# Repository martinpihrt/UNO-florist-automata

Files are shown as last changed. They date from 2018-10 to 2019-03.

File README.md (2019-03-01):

UNO florist automata Readme  
====

## UNO florist automata - Zavlažovač květin je založený na platformě Arduino a desce Arduino UNO<br>
(procesor ATMEGA328 a vlastní deska spojů)

Celý projekt je založen jako volný zdroj (lze použít pro nekomerční použití a přizpůsobit si k obrazu svému).<br>
K řídící desce je připojeno teplotní čidlo DS18B20, které měří teplotu půdy (pro možnost regulace zavlažování dle teploty)<br>
K řídící desce je také připojeno čidlo vlhkosti s frekvenčním výstupem 50Hz-5kHz (pro možnost regulace zavlažování dle vlhkosti) https://pihrt.com/elektronika/272-snimac-vlhkosti-pro-zalevaci-automat<br>
Veškeré nastavení automatu se provádí pomocí tlačítek a zobrazení údajů na 16x2 LCD displeji.<br>
Automat byl vyvinutý pro vertikální zavlažování rostlin, které má svá specifika zavlažování.<br>

## Pro více informací navštivte web...
Martin Pihrt - www.pihrt.com: https://pihrt.com/elektronika/400-uno-florist-automata<br>

## Pohled na desku a připojení čidel
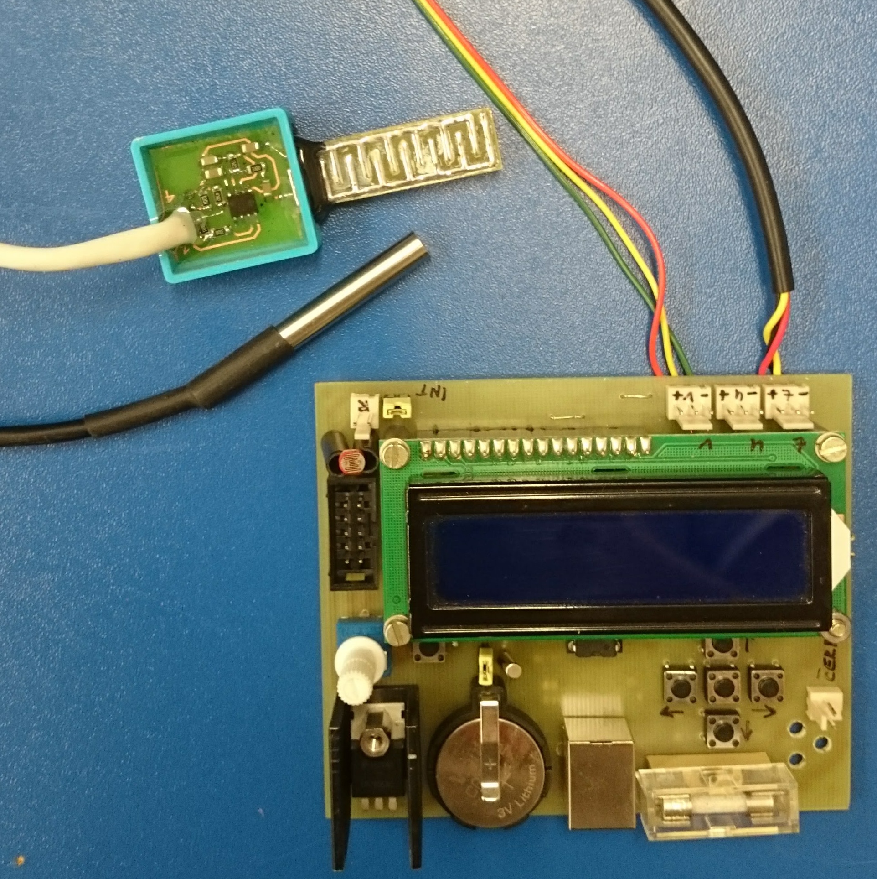
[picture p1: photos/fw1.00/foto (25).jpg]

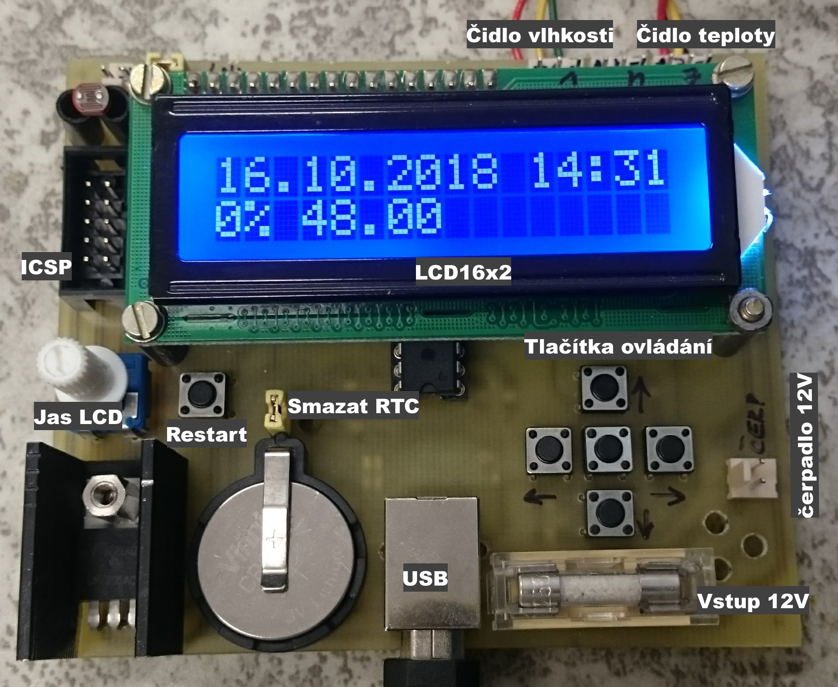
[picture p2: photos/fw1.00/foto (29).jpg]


## Video (fw 1.00 beta)
Ukázka chodu (https://www.pihrt.com/images/videa/automata_1.00.mp4)

## Nastavení zavlažování dle dnů od pondělí do neděle
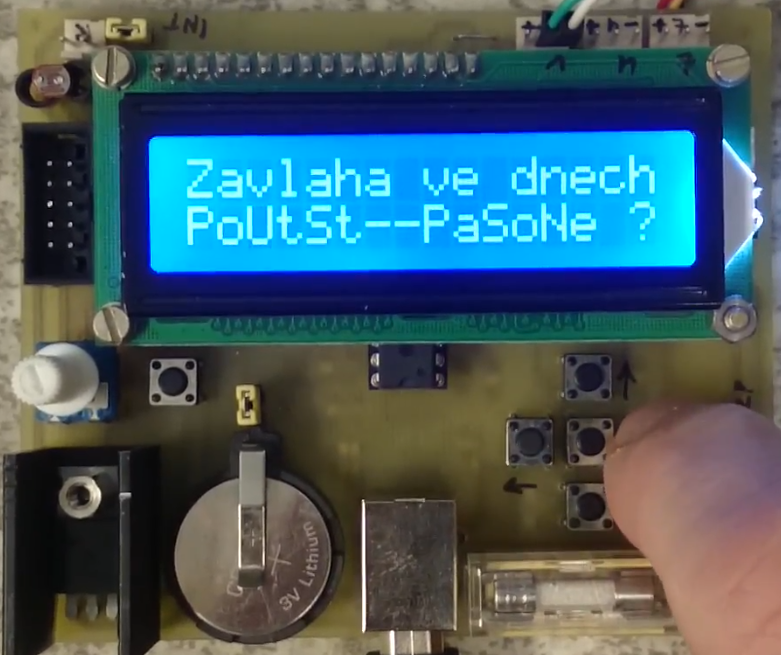
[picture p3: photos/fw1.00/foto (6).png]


## Nastavení 3 nezávislých časů pro zavlažování s různou dobou provozu čerpadla
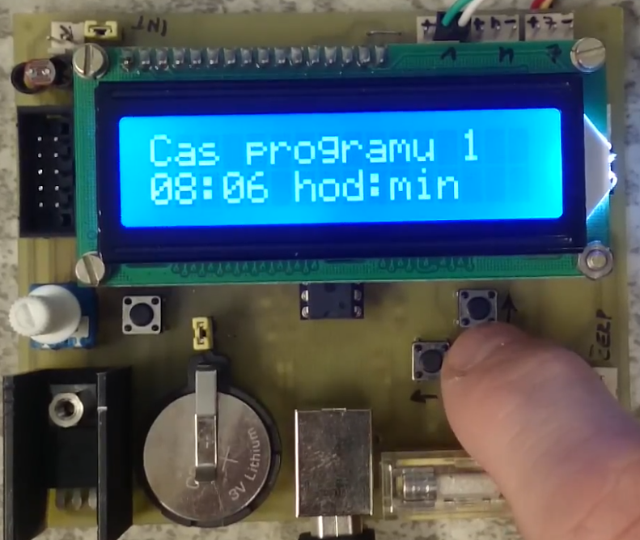
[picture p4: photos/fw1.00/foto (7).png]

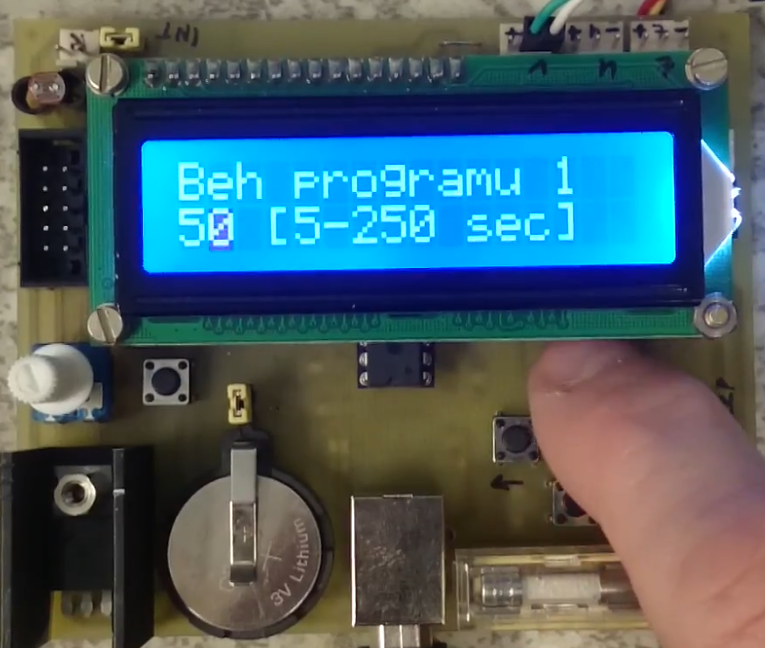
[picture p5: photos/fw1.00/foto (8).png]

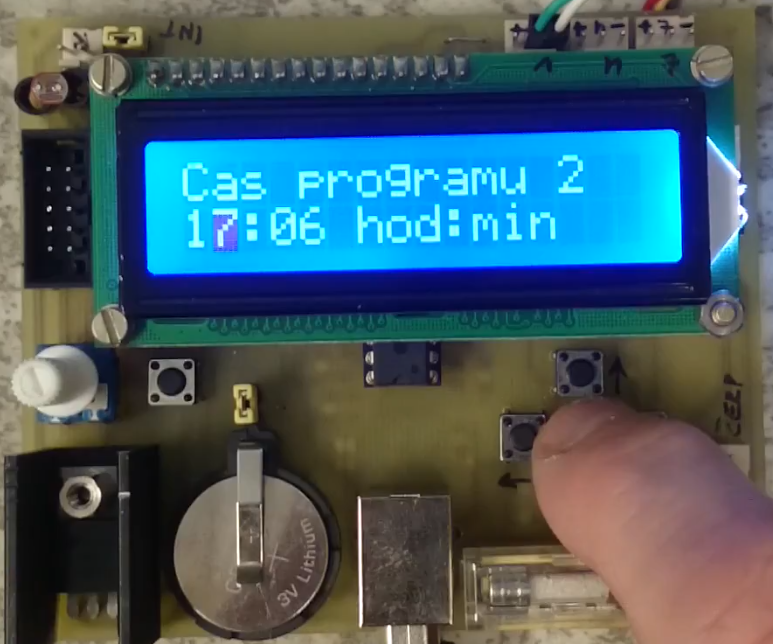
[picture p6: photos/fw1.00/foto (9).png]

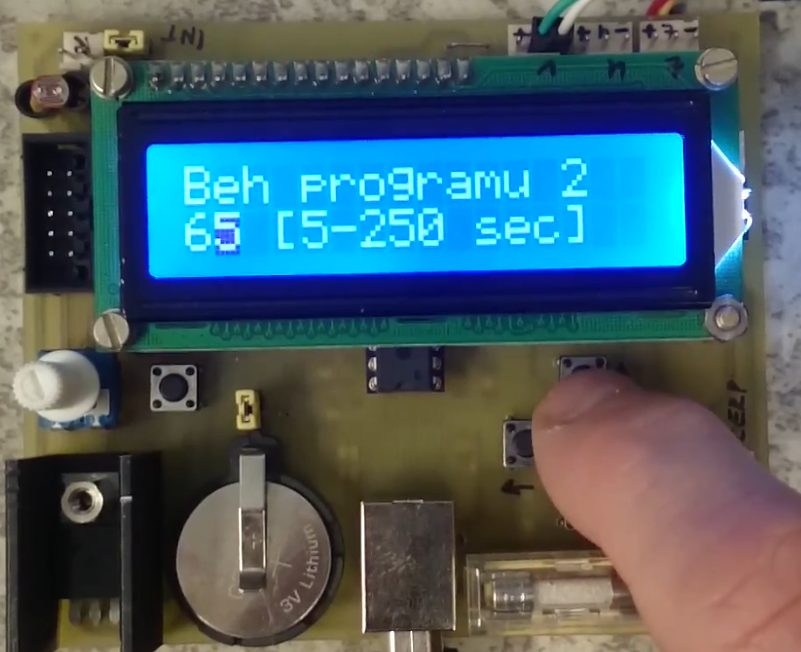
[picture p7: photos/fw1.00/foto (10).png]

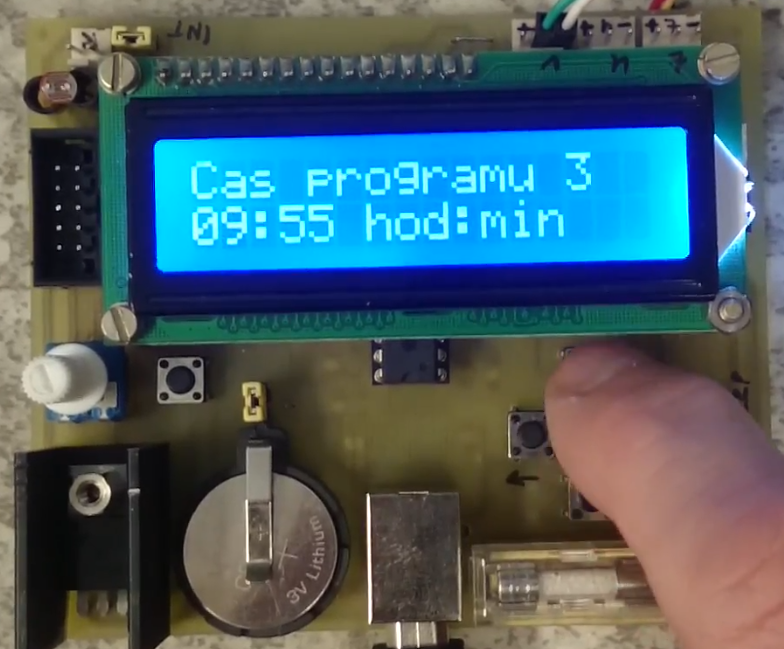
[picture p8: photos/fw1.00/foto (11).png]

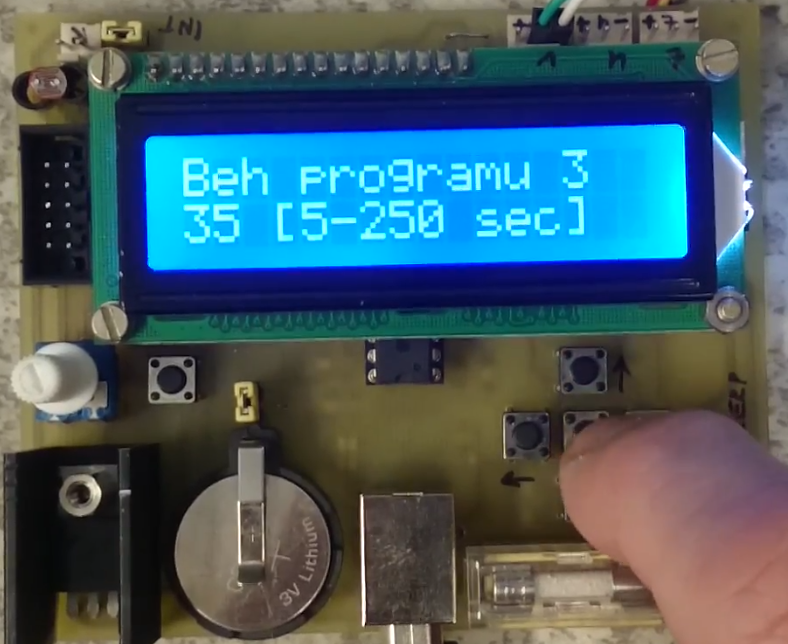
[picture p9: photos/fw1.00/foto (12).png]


## Regulace dle vlhkosti
a) pokud je daný den a je čas programu 1 nebo je čas programu 2 nebo je čas programu 3 a vlhkost < 40% bude výsledná doba trvání závlahy + 1/2 trvání závlahy nastavené doby v menu. Tj. 150% času.<br>
b) pokud je daný den a je čas programu 1 nebo je čas programu 2 nebo je čas programu 3 a vlhkost >= 40% a < 60% bude výsledná doba trvání závlahy stejná jako nastavená doba v menu. Tj. 100% času.<br>
c) pokud je daný den a je čas programu 1 nebo je čas programu 2 a vlhkost >= 60% a < 80% bude výsledná doba trvání závlahy stejná jako nastavená doba v menu. Tj. 100% času.<br>
d) pokud je daný den a je čas programu 1 a vlhkost >= 60% bude výsledná doba trvání závlahy stejná jako nastavená doba v menu. Tj. 100% času.<br>
Z výše uvedeného vyplývá, že některé programy se s ohledem na vlhkost v určitém rozsahu vůbec nespustí, nebo bude výsledný čas upraven.<br>
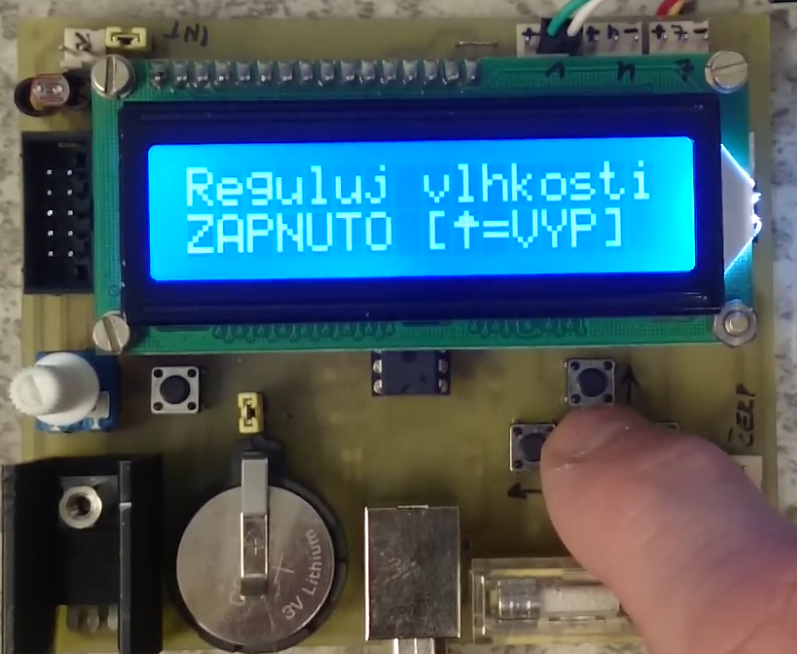
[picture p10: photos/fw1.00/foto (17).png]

<b>V žádném případě nepoužívejte obě regulace současně!</b>

## Regulece dle teploty
a) pokud je daný den a je čas programu 1 nebo je čas programu 2 nebo je čas programu 3 a teplota > 40°C bude výsledná doba trvání závlahy + 1/2 trvání závlahy nastavené doby v menu. Tj. 150% času.<br>
b) pokud je daný den a je čas programu 1 nebo je čas programu 2 nebo je čas programu 3 a teplota >= 30°C a < 40°C bude výsledná doba trvání závlahy stejná jako nastavená doba v menu. Tj. 100% času.<br>
c) pokud je daný den a je čas programu 1 nebo je čas programu 2 a teplota >= 20°C a < 30°C bude výsledná doba trvání závlahy stejná jako nastavená doba v menu. Tj. 100% času.<br>
d) pokud je daný den a je čas programu 1 a teplota >= 5°C a < 20°C bude výsledná doba trvání závlahy stejná jako nastavená doba v menu. Tj. 100% času.<br>
Z výše uvedeného vyplývá, že některé programy se s ohledem na teplotu v určitém rozsahu vůbec nespustí, nebo bude výsledný čas upraven.<br>
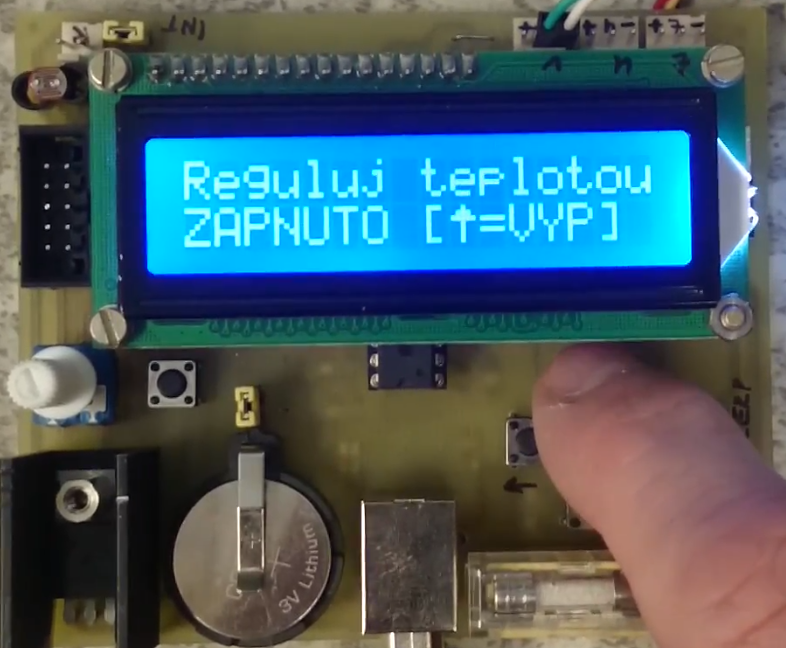
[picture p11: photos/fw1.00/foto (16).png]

<b>V žádném případě nepoužívejte obě regulace současně!</b>

## Cyklování výstupu
V menu lze nastavit po jaké době běhu programu (1, 2, 3) se má výstup čerpadla vypnout a jako dobu má čekat vypnutý. Tato funkce umožňuje cyklování výstupu pro lepší vsakování vody do půdy (nedojde k přetékání květináče, ale k postupnému vsaku vody)<br>
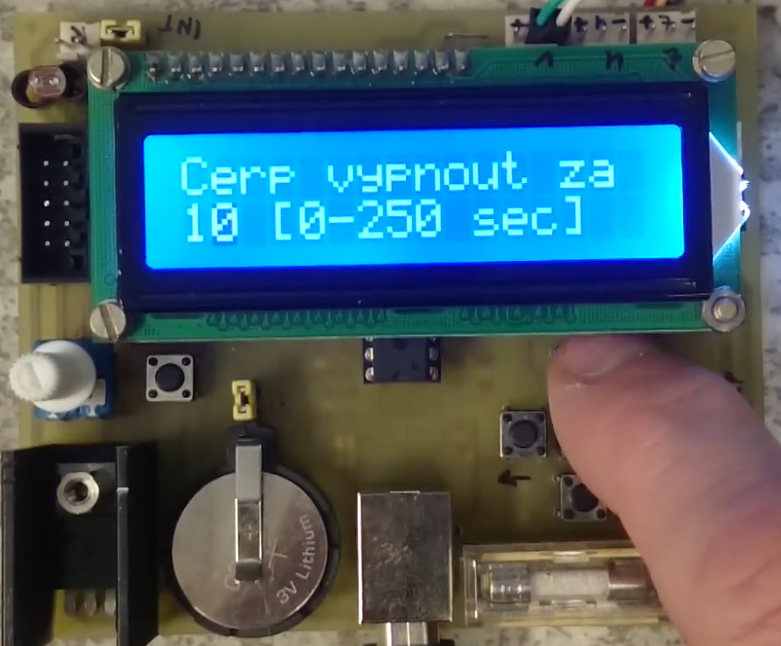
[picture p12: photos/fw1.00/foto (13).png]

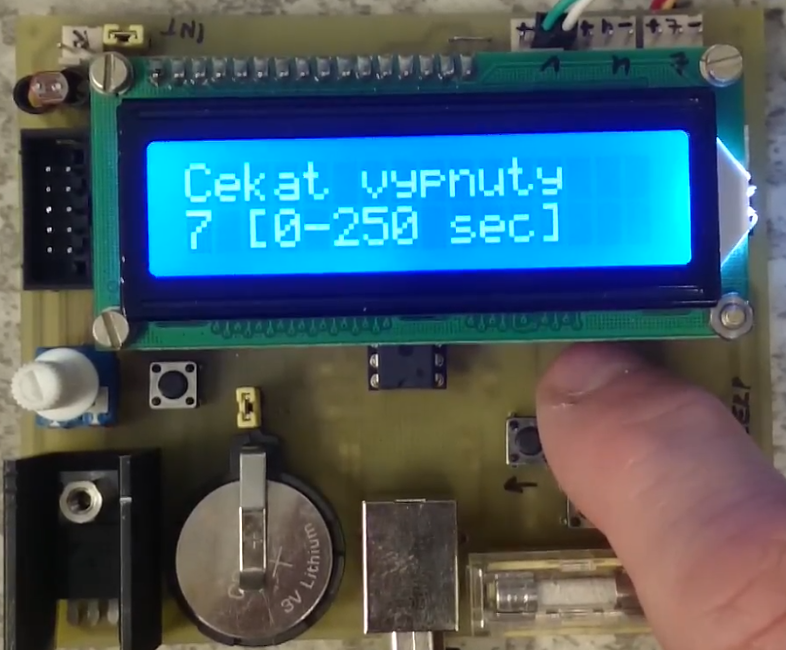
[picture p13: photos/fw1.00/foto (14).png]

Pokud nepožadujeme funkci cyklování nastavíme v menu "vypnout na dobu" na hodnotu 0s" a "vypnout čerpadlo po" na maximální hodnotu 250s.<br>
V grafu je vidět spínání výstupu (zap/vyp cyklování) s ohledem na vlhkost.<br>
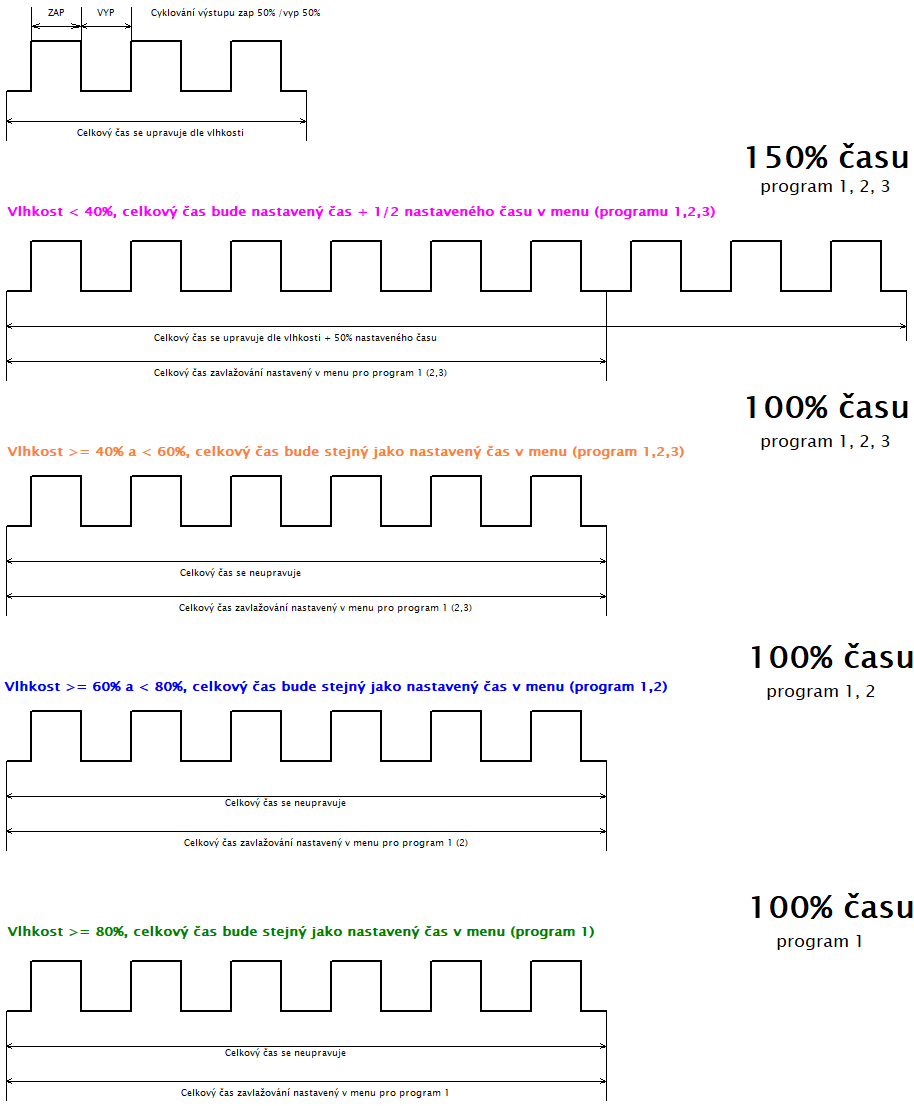
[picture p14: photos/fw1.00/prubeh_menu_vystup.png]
 

## Nastavení datumu a času
Zleva nastavujeme den, měsíc, rok, hodina a minuta. Vteřina se při uložení nastaví na "0". Čas je ukládán do obvodu RTC DS1307.<br>
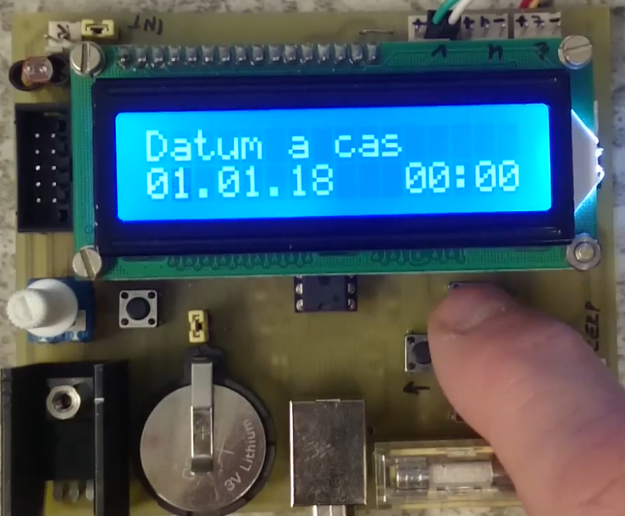
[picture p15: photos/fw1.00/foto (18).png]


## Smazání do továrního nastavení
Pokud chceme zařízení vymazat do továrního nastavení stiskneme v menu jako níže na obrázku "ANO".<br>
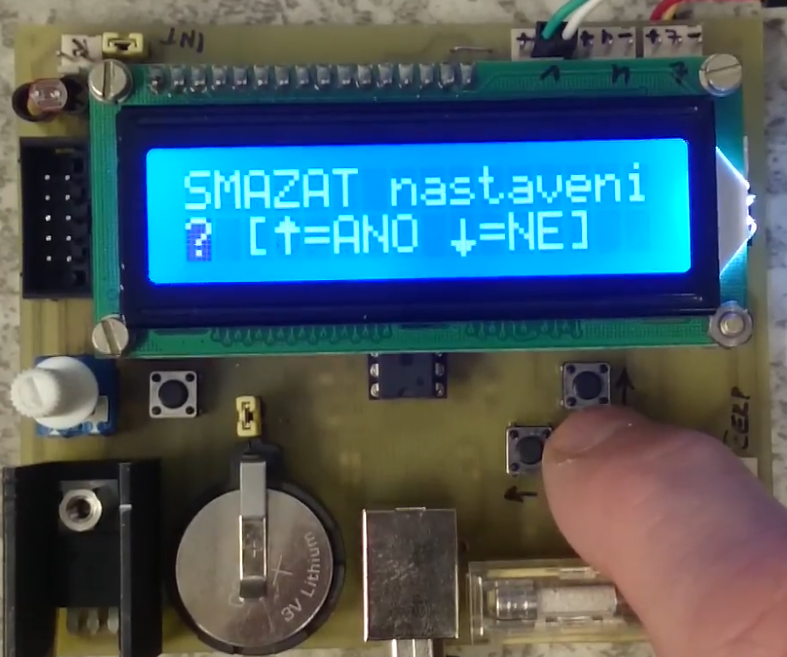
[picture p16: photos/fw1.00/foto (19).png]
<br>
* Výchozí údaje po resetu:<br>
* program 1 čas pro zavlažování 6:00<br>
* doba 30s<br>
* program 2 čas pro zavlažování 18:00<br>
* doba 30s<br>
* program 3 čas pro zavlažování 9:00<br> 
* doba 30s<br>
* vypnout čerpadlo po 5s<br>
* vypnout na dobu 20s<br>
* nepoužívat regulaci teplotou<br>
* nepoužívat regulaci vhlkostí<br>
* zavlažovat ve dnech po-ne<br>

## Uložit nastavení
Všechny parametry se ukládají do trvalé paměti EEPROM.<br>
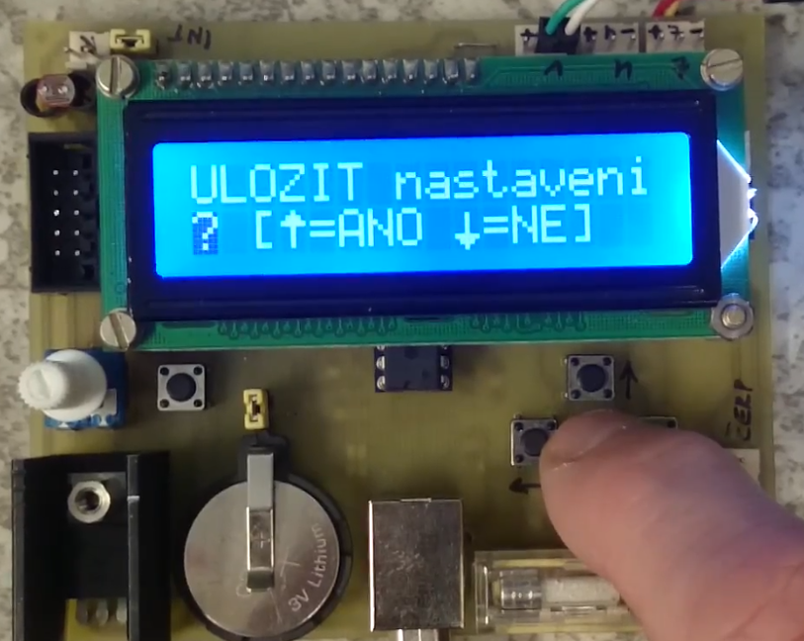
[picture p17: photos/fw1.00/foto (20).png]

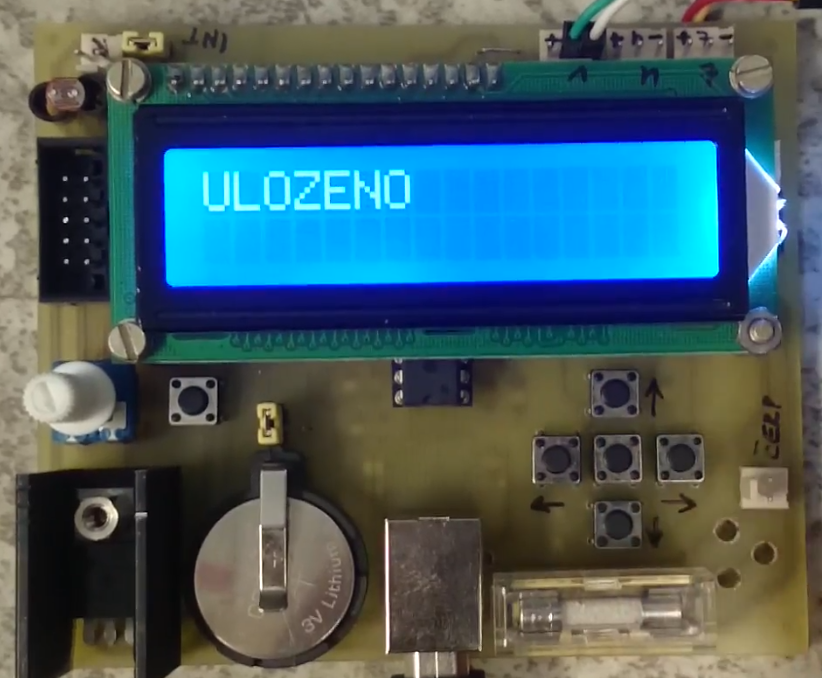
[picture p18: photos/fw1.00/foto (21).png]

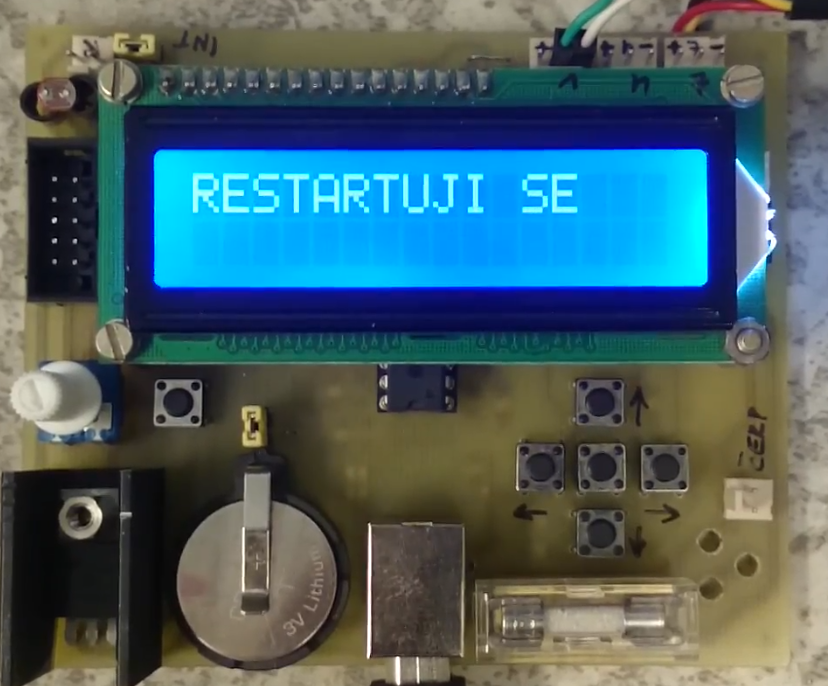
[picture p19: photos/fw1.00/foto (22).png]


## Připojení vstupů a výstupů  
* LCD:                    pin 8, 9,  2,  3,  6,  7 (Rs, E,DB4,DB5,DB6,DB7)<br>
* LCD podsvícení:         pin 10<br>
* Tlačítka IN:            pin 14 (A0 dělič 5 tlačítek)<br>
* Čidlo vlhka IN:         pin 5 (měří se frekvence ze snímače vlhkosti)<br>
* Serial:                 pin 0, 1<br>
* I2C:                    pin 18 (A4 SDA), 19 (A5 SCL) používá DS1307 adr. 0x68<br>
* Teplota:                pin 16  DS18B20 rudá +5V, černá GND, modrá (bílá) Data<br>
* Čerpadlo:               pin 17 (pro výstup - čerpadlo)<br>

## Verze FW, HW
* 1.00 výchozí verze desky a programu (měření vlhkosti pomocí frekvence)
* 1.10 upravená verze HW (přidán konektor na vstup A1) a FW (možnost měření vlhkosti pomocí sondy s napěťovým výstupem) příklad použité sondy: https://www.diymore.cc/products/2pcs-capacitive-soil-moisture-sensor-v1-2-analog-corrosion-resistant-dc-3-3-5-5v)
* 1.11 příprava na podporu více jazyků (zatím není hotové)

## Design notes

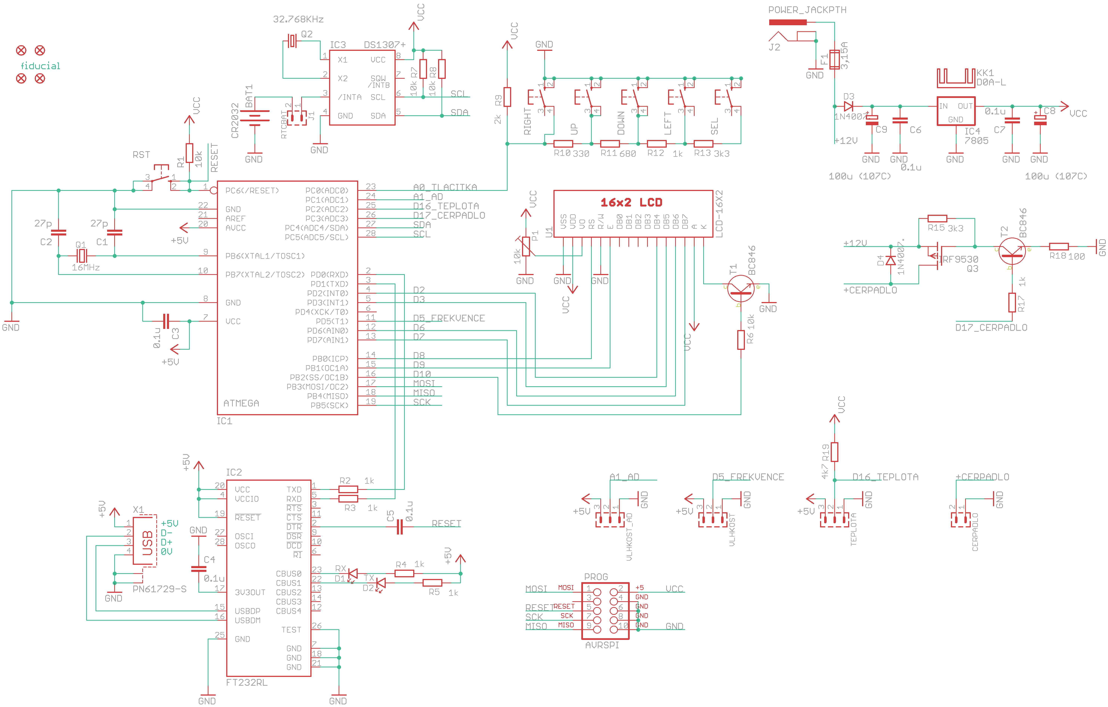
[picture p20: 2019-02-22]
hw/eagle 1.10/schematic.png

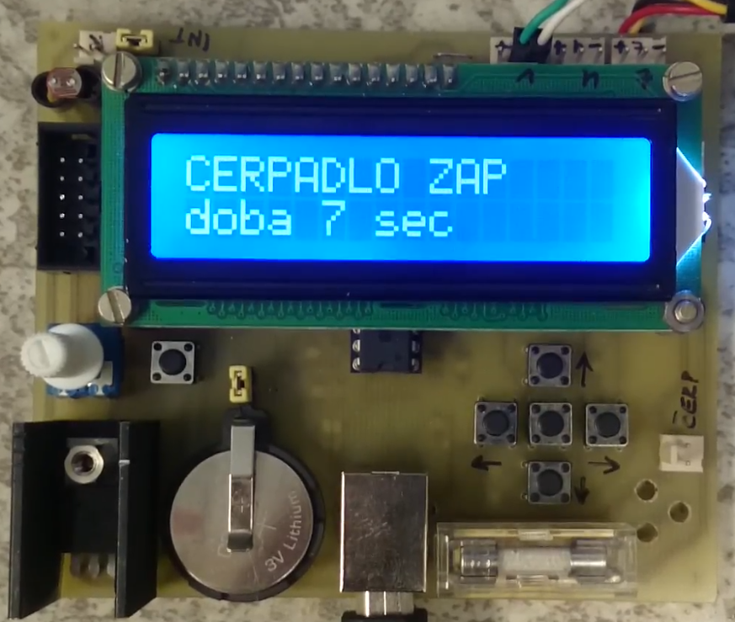
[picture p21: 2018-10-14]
photos/fw1.00/foto (23).png

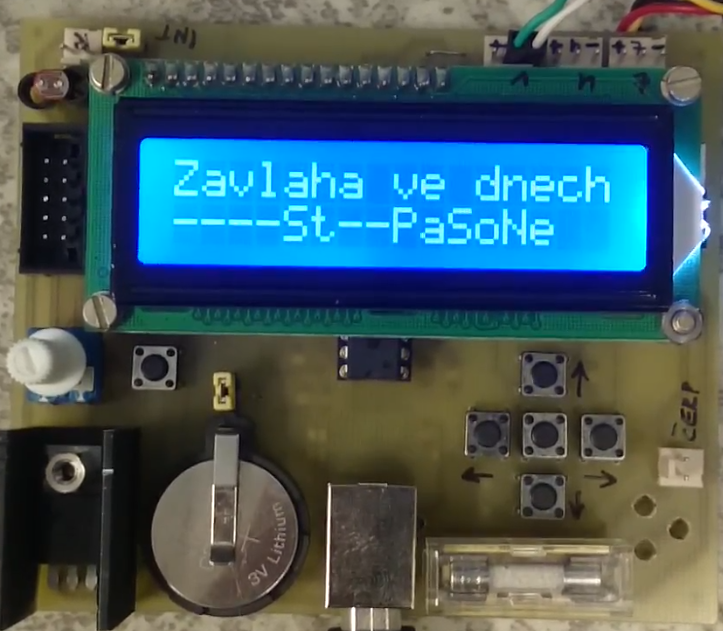
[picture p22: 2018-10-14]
photos/fw1.00/foto (3).png

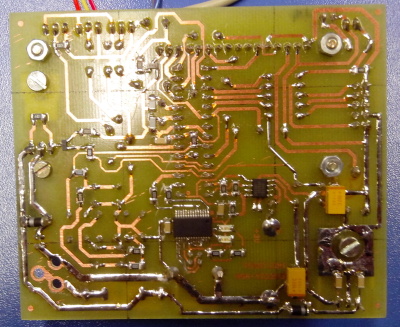
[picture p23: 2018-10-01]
photos/first-version/bot.jpg

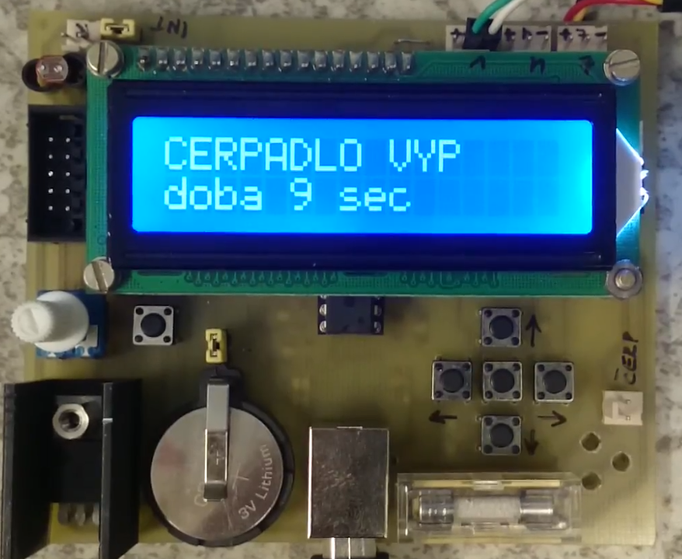
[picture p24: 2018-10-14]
photos/fw1.00/foto (24).png

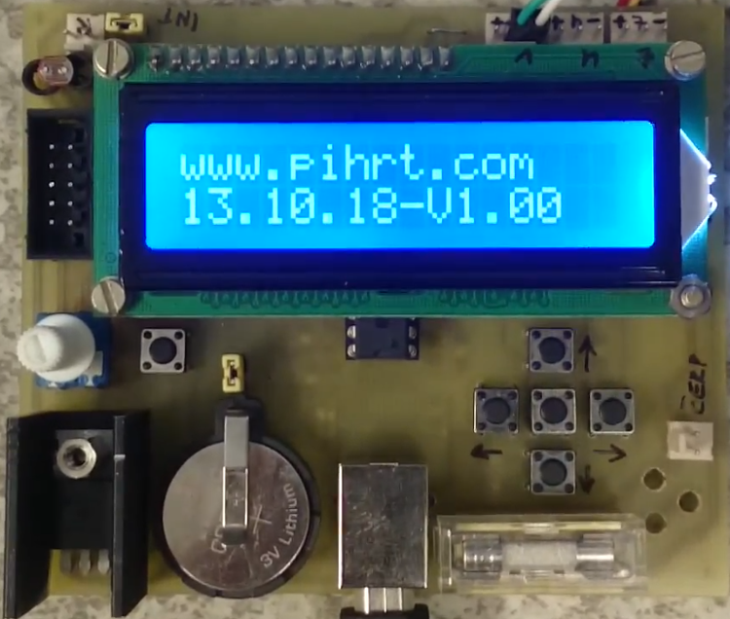
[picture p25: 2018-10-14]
photos/fw1.00/foto (1).png

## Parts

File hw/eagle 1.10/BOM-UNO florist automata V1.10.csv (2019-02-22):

Part | Value | Device | Package | Description | MF | MPN | OC_FARNELL | OC_NEWARK | PROD_ID
BAT1 | CR2032 | BATTERY20PTH | BATTCOM_20MM_PTH | Battery Holders
C1 | 27p | C-EUC1206 | C1206 | CAPACITOR, European symbol
C2 | 27p | C-EUC1206 | C1206 | CAPACITOR, European symbol
C3 | 0.1u | C-EUC1206 | C1206 | CAPACITOR, European symbol
C4 | 0.1u | C-EUC1206 | C1206 | CAPACITOR, European symbol
C5 | 0.1u | C-EUC1206 | C1206 | CAPACITOR, European symbol
C6 | 0.1u | C-EUC1206 | C1206 | CAPACITOR, European symbol
C7 | 0.1u | C-EUC1206 | C1206 | CAPACITOR, European symbol
C8 | 100u (107C) | CPOL-EUC/6032-28W | C/6032-28W | POLARIZED CAPACITOR, European symbol
C9 | 100u (107C) | CPOL-EUC/6032-28W | C/6032-28W | POLARIZED CAPACITOR, European symbol
CERPADLO |  | PSH02-02P | PSH02-02P | Konektory se zamkem - vidlice - 2pin
D1 | RX | LED_1206 | P1206 | LED - jednobarevna
D2 | TX | LED_1206 | P1206 | LED - jednobarevna
D3 | 1N4007. | 1N4007. | SM-1 | Usmernovaci dioda - 1A, 1000V
D4 | 1N4007. | 1N4007. | SM-1 | Usmernovaci dioda - 1A, 1000V
DOWN |  | 10-XX | B3F-10XX | OMRON SWITCH
F1 | 3,15A | FUSE2P | FUSE1 | FUSE
FID1 | FIDUCIAL1.5X3 | FIDUCIAL1.5X3 | FIDUCIAL-1.5X3 | Fiducial Alignment Points
FID2 | FIDUCIAL1.5X3 | FIDUCIAL1.5X3 | FIDUCIAL-1.5X3 | Fiducial Alignment Points
FID3 | FIDUCIAL1.5X3 | FIDUCIAL1.5X3 | FIDUCIAL-1.5X3 | Fiducial Alignment Points
FID4 | FIDUCIAL1.5X3 | FIDUCIAL1.5X3 | FIDUCIAL-1.5X3 | Fiducial Alignment Points
IC1 | ATMEGA | MEGA8-P | DIL28-3 | MICROCONTROLLER
IC2 | FT232RL | FT232RL | SSOP28 | Source: http://www.ftdichip.com/Documents/DataSheets/DS_FT232R_v104.pdf |  | FT232RL | 1146032 | 91K9918
IC3 | DS1307+ | DS1337S+ | SO08 | RTC - obvod realneho casu
IC4 | 7805 | 78XXL | 78XXL | VOLTAGE REGULATOR
J1 | RTCBAT | S1G2_JUMP | S1G2_JUM | Radove konektory - koliky - 2x
J2 | POWER_JACKPTH | POWER_JACKPTH | POWER_JACK_PTH | Power Jack |  |  |  |  | PRT-00119
KK1 | D0A-L | D0A-L | D02A-L | HEATSINK
LEFT |  | 10-XX | B3F-10XX | OMRON SWITCH
P1 | 10k | TRIMRPT10V | PT10V | Trimr
PROG | AVRSPI | AVR_SPI_PROG2LOCK | 2X5-SHROUDED_LOCK | AVR 10-pin ICSP Header
Q1 | 16MHz | Q_HC-49U | HC-49U | Krystal
Q2 | 32.768KHz | CRYSTALTC38H | TC38H | CRYSTAL |  |  | unknown | unknown
Q3 | IRF9530 | IRF9530 | TO220 | P-Channel Enhancement MOSFET (HEXFET); -100V; -12A; 0,3Ohm
R1 | 10k | R-EU_M1206 | M1206 | RESISTOR, European symbol
R2 | 1k | R-EU_M1206 | M1206 | RESISTOR, European symbol
R3 | 1k | R-EU_M1206 | M1206 | RESISTOR, European symbol
R4 | 1k | R-EU_M1206 | M1206 | RESISTOR, European symbol
R5 | 1k | R-EU_M1206 | M1206 | RESISTOR, European symbol
R6 | 10k | R-EU_M1206 | M1206 | RESISTOR, European symbol
R7 | 10k | R-EU_M1206 | M1206 | RESISTOR, European symbol
R8 | 10k | R-EU_M1206 | M1206 | RESISTOR, European symbol
R9 | 2k | R-EU_M1206 | M1206 | RESISTOR, European symbol
R10 | 330 | R-EU_M1206 | M1206 | RESISTOR, European symbol
R11 | 680 | R-EU_M1206 | M1206 | RESISTOR, European symbol
R12 | 1k | R-EU_M1206 | M1206 | RESISTOR, European symbol
R13 | 3k3 | R-EU_M1206 | M1206 | RESISTOR, European symbol
R15 | 3k3 | R-EU_M1206 | M1206 | RESISTOR, European symbol
R17 | 1k | R-EU_M1206 | M1206 | RESISTOR, European symbol
R18 | 100 | R-EU_M1206 | M1206 | RESISTOR, European symbol
R19 | 4k7 | R-EU_M1206 | M1206 | RESISTOR, European symbol
RIGHT |  | 10-XX | B3F-10XX | OMRON SWITCH
RST |  | 10-XX | B3F-10XX | OMRON SWITCH
SEL |  | 10-XX | B3F-10XX | OMRON SWITCH
T1 | BC846 | BC846 | SOT-23 | SMD tranzistor - NPN - ekv. BC546
T2 | BC846 | BC846 | SOT-23 | SMD tranzistor - NPN - ekv. BC546
TEPLOTA |  | PSH02-03P | PSH02-03P | Konektory se zamkem - vidlice - 3pin
U1 | LCD-16X2 | LCD-16X2NOSILK | LCD-16X2_NOSILK | Standard text-only 16x2 parallel input LCD
UP |  | 10-XX | B3F-10XX | OMRON SWITCH
VLHKOST |  | PSH02-03P | PSH02-03P | Konektory se zamkem - vidlice - 3pin
VLHKOST_AD |  | PSH02-03P | PSH02-03P | Konektory se zamkem - vidlice - 3pin
X1 | PN61729-S | PN61729-S | PN61729-S | BERG USB connector |  |  | unknown | unknown

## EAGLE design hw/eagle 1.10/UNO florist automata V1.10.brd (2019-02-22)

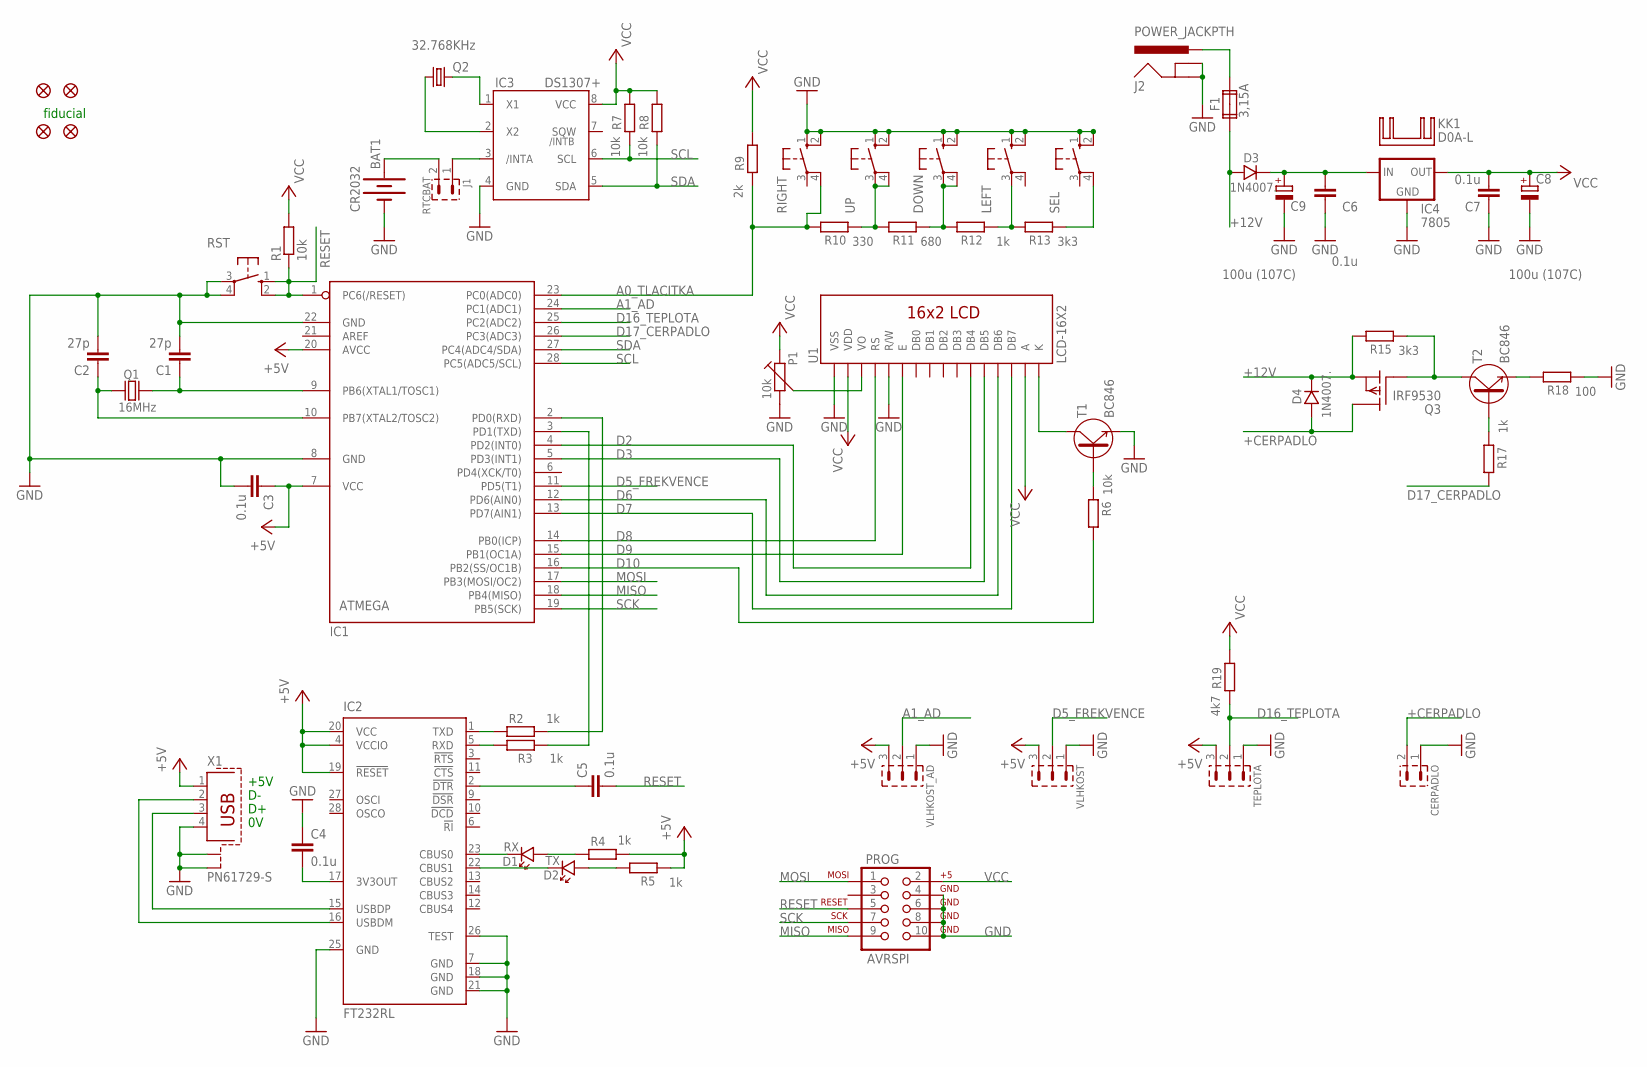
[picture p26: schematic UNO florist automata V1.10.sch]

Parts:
BAT1: CR2032; BATTCOM_20MM_PTH
C1, C2: 27p; C1206
C3, C4, C5, C6, C7: 0.1u; C1206
C8, C9: 100u (107C); C/6032-28W
CERPADLO: PSH02-02P
D1: RX; P1206
D2: TX; P1206
D3, D4: 1N4007.; SM-1
DOWN: 10-XX; B3F-10XX
F1: 3,15A; FUSE1
FID1, FID2, FID3, FID4: FIDUCIAL1.5X3; FIDUCIAL-1.5X3
IC1: ATMEGA; DIL28-3
IC2: FT232RL; SSOP28
IC3: DS1307+; SO08
IC4: 7805; 78XXL
J1: RTCBAT; S1G2_JUM
J2: POWER_JACKPTH; POWER_JACK_PTH
KK1: D0A-L; D02A-L
LEFT: 10-XX; B3F-10XX
P1: 10k; PT10V
PROG: AVRSPI; 2X5-SHROUDED_LOCK
Q1: 16MHz; HC-49U
Q2: 32.768KHz; TC38H
Q3: IRF9530; TO220
R1, R6, R7, R8: 10k; M1206
R2, R3, R4, R5, R12, R17: 1k; M1206
R9: 2k; M1206
R10: 330; M1206
R11: 680; M1206
R13, R15: 3k3; M1206
R18: 100; M1206
R19: 4k7; M1206
RIGHT: 10-XX; B3F-10XX
RST: 10-XX; B3F-10XX
SEL: 10-XX; B3F-10XX
T1, T2: BC846; SOT-23
TEPLOTA: PSH02-03P
U1: LCD-16X2; LCD-16X2_NOSILK
UP: 10-XX; B3F-10XX
VLHKOST: PSH02-03P
VLHKOST_AD: PSH02-03P
X1: PN61729-S

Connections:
+12V: D3.A, D4.K, F1.1A, Q3.3 (S), R15.2
+CERPADLO: CERPADLO.2, D4.A, Q3.2 (D)
A: IC3.2 (X2), Q2.1
A0_TLACITKA: IC1.23 (PC0(ADC0)), R9.1, R10.2, RIGHT.4 (P1)
A1_AD: IC1.24 (PC1(ADC1)), VLHKOST_AD.2
D2: IC1.4 (PD2(INT0)), U1.11 (DB4)
D3: IC1.5 (PD3(INT1)), U1.12 (DB5)
D5_FREKVENCE: IC1.11 (PD5(T1)), VLHKOST.2
D6: IC1.12 (PD6(AIN0)), U1.13 (DB6)
D7: IC1.13 (PD7(AIN1)), U1.14 (DB7)
D8: IC1.14 (PB0(ICP)), U1.4 (RS)
D9: IC1.15 (PB1(OC1A)), U1.6 (E)
D10: IC1.16 (PB2(SS/OC1B)), R6.2
D16_TEPLOTA: IC1.25 (PC2(ADC2)), R19.1, TEPLOTA.2
D17_CERPADLO: IC1.26 (PC3(ADC3)), R17.2
GND: BAT1.2 (-), C1.2, C2.2, C3.2, C4.1, C6.1, C7.1, C8.-, C9.-, CERPADLO.1, DOWN.1 (S), DOWN.2 (S1), IC1.8 (GND), IC1.22 (GND), IC2.7 (GND), IC2.18 (GND), IC2.21 (GND), IC2.25 (GND), IC2.26 (TEST), IC3.4 (GND), IC4.GND, J2.GND, J2.GNDBREAK, LEFT.1 (S), LEFT.2 (S1), P1.2, PROG.4, PROG.6, PROG.8, PROG.10, R18.1, RIGHT.1 (S), RIGHT.2 (S1), RST.3, RST.4 (P1), SEL.1 (S), SEL.2 (S1), T1.2 (E), TEPLOTA.1, U1.1 (VSS), U1.5 (R/W), UP.1 (S), UP.2 (S1), VLHKOST.1, VLHKOST_AD.1, X1.4, X1.S1, X1.S2
MISO: IC1.18 (PB4(MISO)), PROG.9
MOSI: IC1.17 (PB3(MOSI/OC2)), PROG.1
unnamed: IC2.16 (USBDM), X1.2
unnamed: IC2.15 (USBDP), X1.3
unnamed: C4.2, IC2.17 (3V3OUT)
unnamed: IC2.1 (TXD), R2.1
unnamed: IC2.5 (RXD), R3.2
unnamed: IC1.2 (PD0(RXD)), R2.2
unnamed: IC1.3 (PD1(TXD)), R3.1
unnamed: C5.1, IC2.2 (!DTR)
unnamed: D1.K, IC2.23 (CBUS0)
unnamed: D1.A, R4.1
unnamed: D2.K, IC2.22 (CBUS1)
unnamed: D2.A, R5.2
unnamed: BAT1.1 (+), J1.2
unnamed: IC3.3 (/INTA), J1.1
unnamed: T1.3 (C), U1.16 (K)
unnamed: R10.1, R11.2, UP.3, UP.4 (P1)
unnamed: DOWN.3, DOWN.4 (P1), R11.1, R12.2
unnamed: LEFT.3, R12.1, R13.2
unnamed: R13.1, SEL.4 (P1)
unnamed: F1.2A, J2.PWR
unnamed: C1.1, IC1.9 (PB6(XTAL1/TOSC1)), Q1.2
unnamed: C6.2, C9.+, D3.K, IC4.IN
unnamed: R6.1, T1.1 (B)
unnamed: C2.1, IC1.10 (PB7(XTAL2/TOSC2)), Q1.1
unnamed: Q3.1 (G), R15.1, T2.3 (C)
unnamed: R18.2, T2.2 (E)
unnamed: R17.1, T2.1 (B)
unnamed: P1.3, U1.3 (VO)
Q1: IC3.1 (X1), Q2.2
RESET: C5.2, IC1.1 (PC6(/RESET)), PROG.5, R1.1, RST.1 (S), RST.2 (S1)
SCK: IC1.19 (PB5(SCK)), PROG.7
SCL: IC1.28 (PC5(ADC5/SCL)), IC3.6 (SCL), R7.1
SDA: IC1.27 (PC4(ADC4/SDA)), IC3.5 (SDA), R8.1
VCC: C3.1, C7.2, C8.+, IC1.7 (VCC), IC1.20 (AVCC), IC2.4 (VCCIO), IC2.19 (!RESET), IC2.20 (VCC), IC3.8 (VCC), IC4.OUT, P1.1, PROG.2, R1.2, R4.2, R5.1, R7.2, R8.2, R9.2, R19.2, TEPLOTA.3, U1.2 (VDD), U1.15 (A), VLHKOST.3, VLHKOST_AD.3, X1.1

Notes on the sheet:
+5V
fiducial

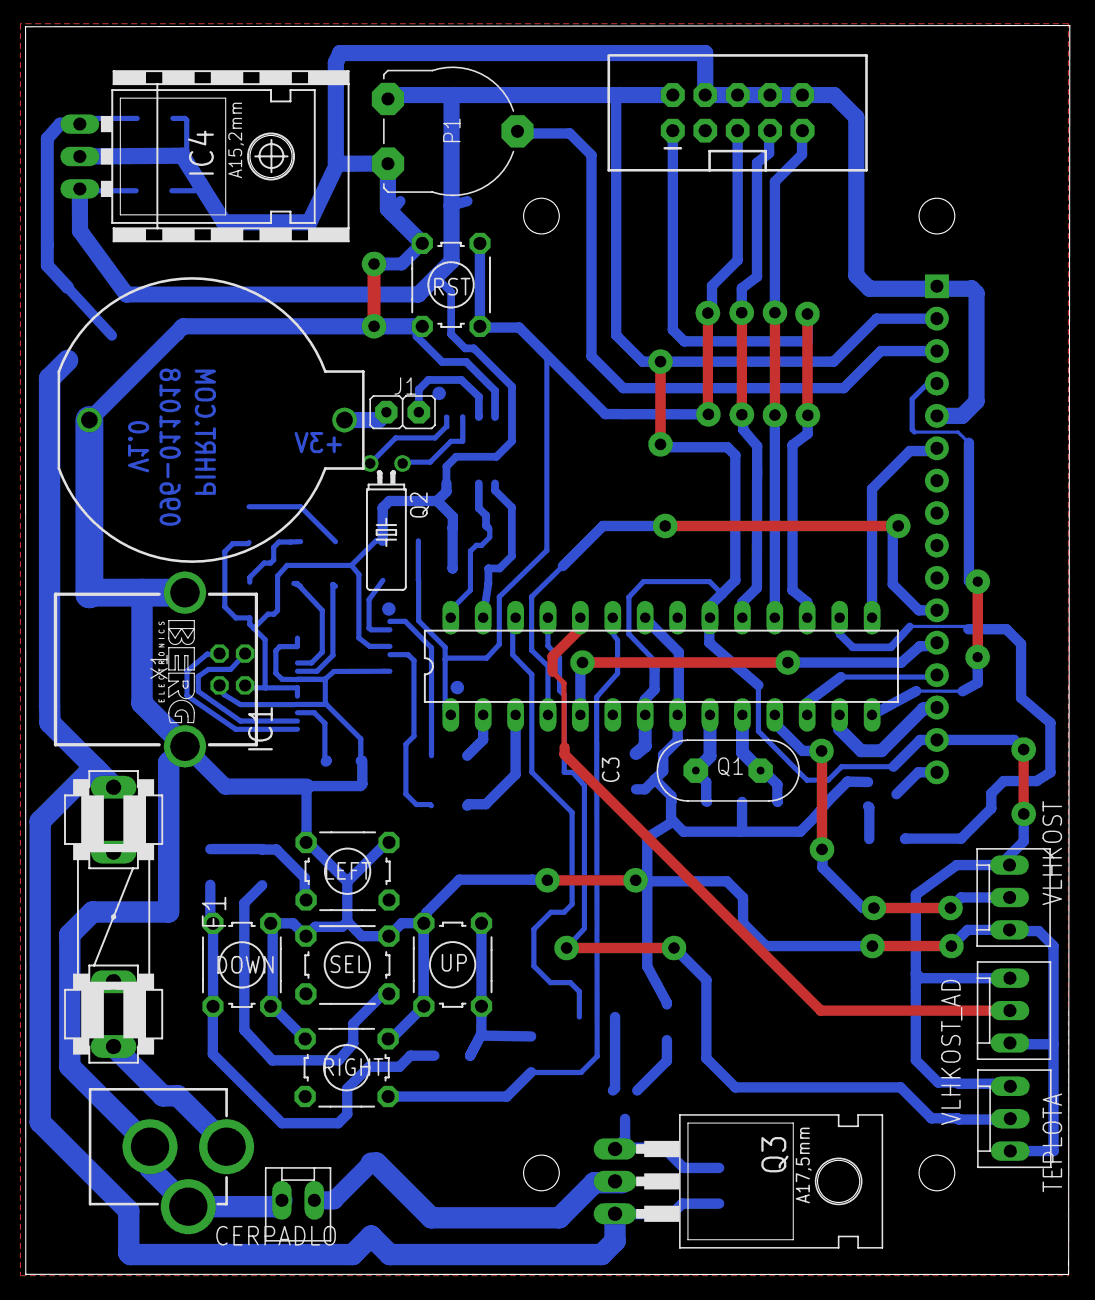
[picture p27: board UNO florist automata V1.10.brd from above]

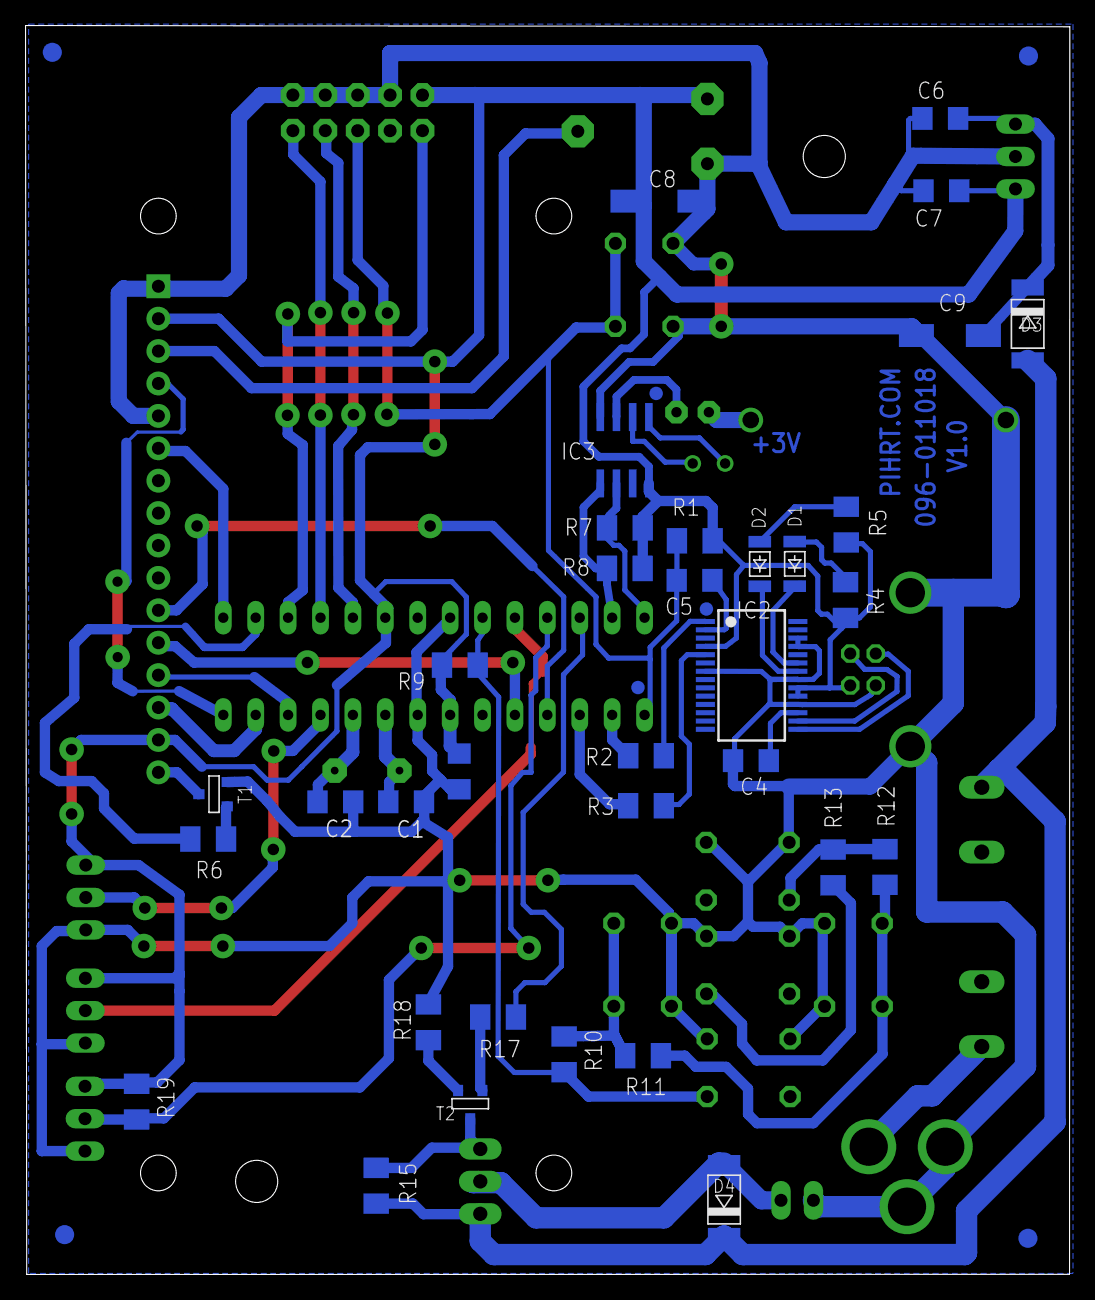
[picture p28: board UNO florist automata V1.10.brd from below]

Board: 2 copper layers, 81.9 x 97.9 mm, 62 parts (38 on the bottom side), 52 nets.

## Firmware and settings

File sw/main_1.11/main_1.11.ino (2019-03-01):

/*

*** MENU *************
? Napoveda
A Spustit program 1
B Spustit program 2
C Spustit program 3
D Nastavit datum a cas
E Smazat EEPROM
F Tisk EEPROM
G Vypsat frekvenci nebo napeti (zalezi na verzi FW)
H Vypsat teplotu
I Vypsat datum a cas
**********************

Vice na www.pihrt.com nebo github

Arduino IDE 1.8.8 www.arduino.cc
Deska UNO (Atmega 328)
verze: avr-gcc\\5.4.0-atmel3.6.1 AVR board 1.6.23
pojistky: efuse:0xFD hfuse:0xDE lfuse:0xFF

                           Rs, E,DB4,DB5,DB6,DB7
LCD:                    pin 8, 9,  2,  3,  6,  7
Serial:                 pin 0, 1
Cidlo vlhka IN:         pin 5 (meri se frekvence ze snimace vlhkosti)
LCD podsviceni:         pin 10
Tlacitka IN:            pin 14 (A0 delic 5 tlacitek)
Cidlo vlhka IN:         pin 15 (A1) meri se napeti ze snimace vlhkosti
Teplota:                pin 16  DS18B20 ruda +5v, cerna GND, modrá(bila) Data
Cerpadlo:               pin 17 (pro motor cerpadla)
I2C:                    pin 18 (A4 SDA), 19 (A5 SCL) pouziva DS1307

adresa I2C:
0x68  DS1307 RTC
*/

/*
 * verze 1.00 
   výchozí verze pouze měření frekvence
 * verze 1.10 
   přidaná možnost měřit vlhkost pomocí frekvence, nebo napětí na AD vstupu (čidlo: https://www.diymore.cc/products/2pcs-capacitive-soil-moisture-sensor-v1-2-analog-corrosion-resistant-dc-3-3-5-5v)
   new features Chris : https://pihrt.com/elektronika/400-uno-florist-automata#comment-370
 * verze 1.11
   přidaná podpora pro více jazyků neni zatim hotove
 */

char verze[]="01.03.19-V1.11"; // Verze programu
#define DEBUG                  // 1/0 Povoleni, nebo zakazani ladeni na serialu
#define baud_rate 115200       // Rychlost serialu nastavit Both NL a CR

// mereni frekvence z cidla vlhkosti
//#define USE_FREQ_PROBE       // Pokud není zakomentované bude se používat měření vlhkosti pomocí frekvence
#define USE_AD_PROBE           // Pokud není zakomentované bude se používat měření vlhkosti pomocí napětí AD převodníku

// freq čidlo
#define cidlo_fMIN     5000    // Hz z cidla pri mokru ve vode
#define cidlo_fMAX     60      // Hz z cidla pri suchu na vzduchu
// napětí čidlo na AD
#define cidlo_AD_min   250     // Cislo 0-1023 na AD převodníku min 
#define cidlo_AD_max   580     // Cislo 0-1023 na AD převodníku max

#define cerpadlo_pin   17      // Cislo pinu pro cerpadlo
#define temp_pin       16      // Cislo pinu cidla teploty
#define lcd_rs         8       // Cisla pinu pro lcd
#define lcd_en         9
#define lcd_db4        2
#define lcd_db5        3
#define lcd_db6        6
#define lcd_db7        7
#define lcd_led        10      // Cislo pinu podsviceni LCD
#define frek_pin       5       // Cislo pinu snimace vlhkosti (vlhkost na frekvenci) na casovaci T1 cpu
#define button_pin     14      // Cislo pinu tlacitek (A0)
#define AD_probe_pin   A1      // Cislo pinu snimace vlhkosti (vlhkost na napeti) vstup A1

#include "LiquidCrystal.h"     // Knihovna LCD displeje
#include "EEPROM.h"            // Knihovna EEPROM
#include "Time.h"              // Cas systemu
#include "Wire.h"              // Knihovna I2C
#include "DS1307RTC.h"         // Knihovna I2C DS1307
#include "OneWire.h"           // Knihovna pro Dallas Temperature OneWire DS18S20, DS18B20, DS1822
#include "DallasTemperature.h" // Knihovna pro rychle mereni teploty bez delay 1000
#include <avr/interrupt.h>     // Knihovna preruseni pro citace frekvence
#include <avr/wdt.h>           // Watchdog
/*watchdog
  wdt_disable();
  wdt_enable(WDTO_15MS); wdt_enable(WDTO_8S); etc
  wdt_reset();
*/

// CZ texty pro LCD a seriový výstup
// deklarace promennych PROGMEM
// aktuálně 79 textů
const char msg_prazdno[]       PROGMEM ="                ";   // msg 0, 16 znaku mezera
const char msg_mezera[]        PROGMEM =" ";                  // msg 1, 1 znak mezera
const char msg_menu0[]         PROGMEM ="Zavlaha ve dnech";   // msg 2, menu 0
const char msg_menu1[]         PROGMEM ="Cas programu 1";     // msg 3, menu 1
const char msg_menu2[]         PROGMEM ="Beh programu 1";     // msg 4, menu 2
const char msg_menu3[]         PROGMEM ="Cas programu 2";     // msg 5, menu 3
const char msg_menu4[]         PROGMEM ="Beh programu 2";     // msg 6, menu 4
const char msg_menu5[]         PROGMEM ="Cas programu 3";     // msg 7, menu 5
const char msg_menu6[]         PROGMEM ="Beh programu 3";     // msg 8, menu 6
const char msg_menu7[]         PROGMEM ="Cerp vypnout za";    // msg 9, menu 7
const char msg_menu8[]         PROGMEM ="Cekat vypnuty";      // msg 10, menu 8
const char msg_menu9[]         PROGMEM ="Reguluj teplotou";   // msg 11, menu 9
const char msg_menu10[]        PROGMEM ="Reguluj vlhkosti";   // msg 12, menu 10
const char msg_menu11[]        PROGMEM ="Datum a cas";        // msg 13, menu 11
const char msg_menu12[]        PROGMEM ="SMAZAT nastaveni";   // msg 14, menu 12
const char msg_menu13[]        PROGMEM ="ULOZIT nastaveni";   // msg 15, menu 13
const char msg_ZAPNUTO[]       PROGMEM ="ZAPNUTO";            // msg 16, pouzito v menu 9, 10, 12, 13
const char msg_VYPNUTO[]       PROGMEM ="VYPNUTO";            // msg 17, pouzito v menu 9, 10, 12, 13
const char msg_VYP[]           PROGMEM ="VYP";                // msg 18, pouzito v menu 9, 10
const char msg_ZAP[]           PROGMEM ="ZAP";                // msg 19, pouzito v menu 9, 10
const char msg_dvojtecka[]     PROGMEM =":";                  // msg 20, pouzito v menu 1, 3, 5
const char msg_rovnase[]       PROGMEM ="=";                  // msg 21,
const char msg_procenta[]      PROGMEM ="%";                  // msg 22,
const char msg_volt[]          PROGMEM ="V";                  // msg 23, 
const char msg_Hz[]            PROGMEM ="Hz";                 // msg 24,
const char msg_kHz[]           PROGMEM ="kHz";                // msg 25,
const char msg_err_cidla[]     PROGMEM ="Chyba cidla";        // msg 26,
const char msg_AD_range[]      PROGMEM ="0-1023";             // msg 27,
const char msg_tecka[]         PROGMEM =".";                  // msg 28,
const char msg_zavL[]          PROGMEM ="[";                  // msg 29,
const char msg_zavP[]          PROGMEM ="]";                  // msg 30,
const char msg_otaznik[]       PROGMEM ="?";                  // msg 31,
const char msg_minus[]         PROGMEM ="-";                  // msg 32,
const char msg_lomitko[]       PROGMEM ="/";                  // msg 33,
const char msg_ANO[]           PROGMEM ="ANO";                // msg 34, 
const char msg_NE[]            PROGMEM ="NE";                 // msg 35,
const char msg_po[]            PROGMEM ="Po";                 // msg 36, 
const char msg_ut[]            PROGMEM ="Ut";                 // msg 37,
const char msg_st[]            PROGMEM ="St";                 // msg 38,
const char msg_ct[]            PROGMEM ="Ct";                 // msg 39,
const char msg_pa[]            PROGMEM ="Pa";                 // msg 40,
const char msg_so[]            PROGMEM ="So";                 // msg 41, 
const char msg_ne[]            PROGMEM ="Ne";                 // msg 42, 
const char msg_dnes[]          PROGMEM ="Dnes je";            // msg 43,
const char msg_pondeli[]       PROGMEM ="pondeli";            // msg 44, 
const char msg_utery[]         PROGMEM ="utery";              // msg 45,
const char msg_streda[]        PROGMEM ="streda";             // msg 46, 
const char msg_ctvrtek[]       PROGMEM ="ctvrtek";            // msg 47,
const char msg_patek[]         PROGMEM ="patek";              // msg 48,
const char msg_sobota[]        PROGMEM ="sobota";             // msg 49,
const char msg_nedele[]        PROGMEM ="nedele";             // msg 50,
const char msg_hod_min[]       PROGMEM ="hod:min";            // msg 51,
const char msg_sec[]           PROGMEM ="sec";                // msg 52,
const char msg_interval_A[]    PROGMEM ="5-250";              // msg 53,
const char msg_interval_B[]    PROGMEM ="0-250";              // msg 54,
const char msg_ulozeno[]       PROGMEM ="ULOZENO";            // msg 55, 
const char msg_rbt[]           PROGMEM ="RESTARTUJI SE";      // msg 56,
const char msg_run_now[]       PROGMEM ="BEZI PROGRAM...";    // msg 57,
const char msg_rtc[]           PROGMEM ="RTC NENALEZEN!";     // msg 58, nenasel na I2C 0x68
const char msg_rtc_run[]       PROGMEM ="CAS NENASTAVEN!";    // msg 59, vraci 165:165:165 165.165.2165
const char msg_cerpadlo[]      PROGMEM ="CERPADLO";           // msg 60,
const char msg_vloz[]          PROGMEM ="Vloz";               // msg 61,
const char msg_doba[]          PROGMEM ="doba";               // msg 62,
const char msg_chyba_dne[]     PROGMEM ="CHYBA RTC!";         // msg 63,
const char msg_cas[]           PROGMEM ="CAS";                // msg 64,  
const char msg_jedna[]         PROGMEM ="1";                  // msg 65,
const char msg_dva[]           PROGMEM ="2";                  // msg 66,
const char msg_tri[]           PROGMEM ="3";                  // msg 67,
const char msg_last_T[]        PROGMEM ="Posledni teplota";   // msg 68,
const char msg_last_V[]        PROGMEM ="Posledni vlhkost";   // msg 69,
const char msg_EE_del[]        PROGMEM ="EEPROM smazana";     // msg 70,
const char msg_menu[]          PROGMEM ="MENU";               // msg 71,
const char msg_dwn[]           PROGMEM ="DOLU";               // msg 72,
const char msg_up[]            PROGMEM ="NAHORU";             // msg 73,
const char msg_left[]          PROGMEM ="VLEVO";              // msg 74,
const char msg_right[]         PROGMEM ="VPRAVO";             // msg 75,
const char msg_end[]           PROGMEM ="Konec";              // msg 76,
const char msg_language[]      PROGMEM ="Jazyk";              // msg 77, 
const char msg_czech[]         PROGMEM ="Cestina";            // msg 78,
const char msg_english[]       PROGMEM ="Anglictina";         // msg 79,

// EN messages for LCD and serial output
// deklaration in PROGMEM
const char msg_en_prazdno[]    PROGMEM ="                ";   // 16 znaku mezera
const char msg_en_mezera[]     PROGMEM =" ";                  // 1 znak mezera
const char msg_en_menu0[]      PROGMEM ="Irrigation days";    // menu 0
const char msg_en_menu1[]      PROGMEM ="Time program 1";     // menu 1
const char msg_en_menu2[]      PROGMEM ="Run program 1";      // menu 2
const char msg_en_menu3[]      PROGMEM ="Time program 2";     // menu 3
const char msg_en_menu4[]      PROGMEM ="Run program 2";      // menu 4
const char msg_en_menu5[]      PROGMEM ="Time program 3";     // menu 5
const char msg_en_menu6[]      PROGMEM ="Run program 3";      // menu 6
const char msg_en_menu7[]      PROGMEM ="Pump off for";       // menu 7
const char msg_en_menu8[]      PROGMEM ="Wait off for";       // menu 8
const char msg_en_menu9[]      PROGMEM ="Reg temperature";    // menu 9
const char msg_en_menu10[]     PROGMEM ="Reg moisture";       // menu 10
const char msg_en_menu11[]     PROGMEM ="Date and time";      // menu 11
const char msg_en_menu12[]     PROGMEM ="DELETE setting";     // menu 12
const char msg_en_menu13[]     PROGMEM ="SAVE settings";      // menu 13
const char msg_en_ZAPNUTO[]    PROGMEM ="is ON";              // pouzito v menu 9, 10, 12, 13
const char msg_en_VYPNUTO[]    PROGMEM ="is OFF";             // pouzito v menu 9, 10, 12, 13
const char msg_en_VYP[]        PROGMEM ="OFF";                // pouzito v menu 9, 10
const char msg_en_ZAP[]        PROGMEM ="ON";                 // pouzito v menu 9, 10
const char msg_en_dvojtecka[]  PROGMEM =":";                  // pouzito v menu 1, 3, 5
const char msg_en_rovnase[]    PROGMEM ="=";
const char msg_en_procenta[]   PROGMEM ="%";
const char msg_en_volt[]       PROGMEM ="V";
const char msg_en_Hz[]         PROGMEM ="Hz";
const char msg_en_kHz[]        PROGMEM ="kHz";
const char msg_en_err_cidla[]  PROGMEM ="Error probe";
const char msg_en_AD_range[]   PROGMEM ="0-1023";
const char msg_en_tecka[]      PROGMEM =".";
const char msg_en_zavL[]       PROGMEM ="[";
const char msg_en_zavP[]       PROGMEM ="]";
const char msg_en_otaznik[]    PROGMEM ="?";
const char msg_en_minus[]      PROGMEM ="-";
const char msg_en_lomitko[]    PROGMEM ="/";
const char msg_en_ANO[]        PROGMEM ="YES";
const char msg_en_NE[]         PROGMEM ="No";
const char msg_en_po[]         PROGMEM ="Mo";
const char msg_en_ut[]         PROGMEM ="Tu";
const char msg_en_st[]         PROGMEM ="We";
const char msg_en_ct[]         PROGMEM ="Th";
const char msg_en_pa[]         PROGMEM ="Fr";
const char msg_en_so[]         PROGMEM ="Sa";
const char msg_en_ne[]         PROGMEM ="Su";
const char msg_en_dnes[]       PROGMEM ="Today is";
const char msg_en_pondeli[]    PROGMEM ="Monday";
const char msg_en_utery[]      PROGMEM ="Tuesday";
const char msg_en_streda[]     PROGMEM ="Wednesday";
const char msg_en_ctvrtek[]    PROGMEM ="Thursday";
const char msg_en_patek[]      PROGMEM ="Friday";
const char msg_en_sobota[]     PROGMEM ="Saturday";
const char msg_en_nedele[]     PROGMEM ="Sunday";
const char msg_en_hod_min[]    PROGMEM ="hour:min";
const char msg_en_sec[]        PROGMEM ="sec";
const char msg_en_interval_A[] PROGMEM ="5-250";
const char msg_en_interval_B[] PROGMEM ="0-250";
const char msg_en_ulozeno[]    PROGMEM ="SAVED";
const char msg_en_rbt[]        PROGMEM ="RESTARTING";
const char msg_en_run_now[]    PROGMEM ="RUN PROGRAM...";
const char msg_en_rtc[]        PROGMEM ="RTC not find!";  // not find rtc on I2C 0x68 address
const char msg_en_rtc_run[]    PROGMEM ="TIME not set!";  // return 165:165:165 165.165.2165
const char msg_en_cerpadlo[]   PROGMEM ="PUMP";
const char msg_en_vloz[]       PROGMEM ="Insert";
const char msg_en_doba[]       PROGMEM ="time";
const char msg_en_chyba_dne[]  PROGMEM ="ERROR RTC!";
const char msg_en_cas[]        PROGMEM ="TIME";
const char msg_en_jedna[]      PROGMEM ="1";
const char msg_en_dva[]        PROGMEM ="2";
const char msg_en_tri[]        PROGMEM ="3";
const char msg_en_last_T[]     PROGMEM ="Last temperature";
const char msg_en_last_V[]     PROGMEM ="Last moisture";
const char msg_en_EE_del[]     PROGMEM ="EEPROM deleted";
const char msg_en_menu[]       PROGMEM ="MENU";
const char msg_en_dwn[]        PROGMEM ="DOWN";
const char msg_en_up[]         PROGMEM ="UP";
const char msg_en_left[]       PROGMEM ="LEFT";
const char msg_en_right[]      PROGMEM ="RIGHT";
const char msg_en_end[]        PROGMEM ="END";
const char msg_en_language[]   PROGMEM ="Language";
const char msg_en_czech[]      PROGMEM ="Czech";
const char msg_en_english[]    PROGMEM ="English";

const char* const text_table[] PROGMEM = { // textova tabulka s CZ texty
  msg_prazdno, msg_mezera, msg_menu0, msg_menu1, msg_menu2, msg_menu3, msg_menu4, msg_menu5, msg_menu6, msg_menu7, msg_menu8, msg_menu9, msg_menu10, msg_menu11, msg_menu12, msg_menu13,
  msg_ZAPNUTO, msg_VYPNUTO, msg_VYP, msg_ZAP, msg_dvojtecka, msg_rovnase, msg_procenta, msg_volt, msg_Hz, msg_kHz, msg_err_cidla, msg_AD_range, msg_tecka, msg_zavL, msg_zavP, msg_otaznik,
  msg_minus, msg_lomitko, msg_ANO, msg_NE, msg_po, msg_ut, msg_st, msg_ct, msg_pa, msg_so, msg_ne, msg_dnes, msg_pondeli, msg_utery, msg_streda, msg_ctvrtek, msg_patek, msg_sobota, msg_nedele, 
  msg_hod_min, msg_sec, msg_interval_A, msg_interval_B, msg_ulozeno, msg_rbt, msg_run_now, msg_rtc, msg_rtc_run, msg_cerpadlo, msg_vloz, msg_doba, msg_chyba_dne, msg_cas, msg_jedna, msg_dva, 
  msg_tri, msg_last_T, msg_last_V, msg_EE_del, msg_menu, msg_dwn, msg_up, msg_left, msg_right, msg_end, msg_language, msg_czech, msg_english                            
};
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
void loop() {

  casovacLCD();                // vypisuje na LCD stavova okna po xx sec
  cti_serial();                // serial_rx_tx (komunikace se serialem)
  cti_klavesnici();            // klavesnice (vyhodnocujeme klavesy)

  if (save) {save_eeprom();}   // ulozi do pameti z lcd menu tlacitek
  else if(!menu) {//neni aktivni menu

     cti_cas_datum();
     Mereni();              // nacte teplotu a vlhkost
     regulace_vlhk();       // zpracuje zavlazovani dle vhlkosti
     regulace_tepl();       // zpracuje zavlažování dle teploty
     cerpadlo();            // zpracuj cerpadlo

     if((hour()==cas1_hod)&&(minute()==cas1_min)&&(second()<5)&& !CAS1) ZavlahaCas(1); // pokud je cas povolime zavlazovani pgm1
     if((hour()==cas2_hod)&&(minute()==cas2_min)&&(second()<5)&& !CAS2) ZavlahaCas(2); // pokud je cas povolime zavlazovani pgm2
     if((hour()==cas3_hod)&&(minute()==cas3_min)&&(second()<5)&& !CAS3) ZavlahaCas(3); // pokud je cas povolime zavlazovani pgm3
  }//end else

  wdt_reset();
} // end loop

void ZavlahaCas(byte pgm){ // je
#ifdef DEBUG
   Serial.print(msg_cas);Serial.print(text_progmem(1));Serial.print(pgm);Serial.print(text_progmem(1));
#endif
   if(pgm==1) {trvani_doby = doba1; CAS1 = true;} // prave je cas 1
   else if(pgm==2) {trvani_doby = doba2; CAS2 = true;} // prave je cas 2
   else if(pgm==3) {trvani_doby = doba3; CAS3 = true;} // prave je cas 3
   else return;
   predchoziCasCerpadlo = millis(); // ulozime aktualni cas pro cerpadlo
   interval = 0;                    // interval cyklovani cerpadla
   predchoziCasDoba = millis();     // interval doby zalevani 
#ifdef DEBUG
   Serial.print(msg_doba);Serial.print(text_progmem(1));Serial.print(trvani_doby);Serial.print(text_progmem(1));Serial.println(msg_sec);
#endif      
} // end void

void casovacLCD(){         // posouva pomalu text na lcd
  if(!menu){               // kdyz neni menu
    if(!cerpadlo_makej){   // nejede program
      LCDinterval = 3000;  // 3 vteriny posun textu na LCD
      if (millis() - LCDMillis >= LCDinterval){
        LCDMillis = millis();
        posun_lcd++;
        vypisuj_info_lcd();
      }//end millis
    }//end makej
    else{ // jede program
      LCDinterval = 1000; // vterina posun textu s casem na LCD
        if (millis() - LCDMillis >= LCDinterval){
          LCDMillis = millis();
          lcd.setCursor(0,0);
          lcd.print(msg_cerpadlo);
          lcd.print(text_progmem(1));
          if(cerpadlo_vystup_stav) {
            lcd.print(msg_VYP); lcd.print(text_progmem(0));lcd.setCursor(0,1);lcd.print(msg_doba);lcd.print(text_progmem(1));
            }
          else{
            lcd.print(msg_ZAP); lcd.print(text_progmem(0));lcd.setCursor(0,1);lcd.print(msg_doba);lcd.print(text_progmem(1));
            }
          odpocet_cerpadlo = ((predchoziCasCerpadlo+interval)-aktualniCasCerpadlo)/1000; // cas v sec misto ms
          // zobrazi na LCD cas v sec zap nebo vyp a celkovy cas programu (pr: 5/254sec)
          lcd.print(odpocet_cerpadlo);lcd.print(msg_lomitko);lcd.print(aktualniCasDoba/1000-predchoziCasDoba/1000);lcd.print(msg_sec); 
          lcd.print(text_progmem(0));
        }//end millis
    }//end makej
  }//end if
}//end void

void Mereni(){ // meri teplotu a frekvenci pokud neni aktivni menu a nebezi program 1-3
  if (!menu && !CAS1 && !CAS2 && !CAS3){
    cti_teplotu();       // ds18b20
    #ifdef USE_FREQ_PROBE
      cti_frekvenci();   // freq snimac vlhkosti
    #endif  
    
    #ifdef USE_AD_PROBE
      cti_napeti();      // napeti snimac vhlkosti
    #endif  
  }
  
  #ifdef USE_FREQ_PROBE
     vlhkost = mapuj(frq,cidlo_fMIN,cidlo_fMAX,100,0); // prevod frekvence na vlhkost stupnice vlhka 0-100 s ohledem na min a max frekvenci z cidla
  #endif
  #ifdef USE_AD_PROBE
     AD_in   = mapuj(AD_in,0,1023,cidlo_AD_min,cidlo_AD_max);  // prevod 0-1023 z cidla na rozsah cidlo_AD_min,cidlo_AD_max
    // Serial.print(AD_in);Serial.print(",");
     vlhkost = mapuj(AD_in,cidlo_AD_min,cidlo_AD_max,100,0);   // prevod cidlo_AD_min,cidlo_AD_max na 0-100 vlhkost
    // Serial.println(vlhkost);
  #endif
      
  if(vlhkost >= 100)  vlhkost = 100;  
  if(vlhkost <1)   vlhkost = 0;
} // end void

void cti_frekvenci(){
#ifdef USE_FREQ_PROBE  
  //------------------------------------------
  // http://www.gammon.com.au/forum/?id=11504

// stop Timer 0 interrupts from throwing the count out
  //byte oldTCCR0A = TCCR0A;
  //byte oldTCCR0B = TCCR0B;
  //TCCR0A = 0;    // stop timer 0
  //TCCR0B = 0;

  startCounting (500);  // how many ms to count for
  while (!counterReady){
    wdt_reset();
  }
  // adjust counts by counting interval to give frequency in Hz
  frq = (timerCounts * 1000.0) / timerPeriod;
  // restart timer 0
  //TCCR0A = oldTCCR0A;
  //TCCR0B = oldTCCR0B;
#endif
} // end void

void cti_napeti(){
    #ifdef USE_AD_PROBE
      AD_in = analogRead(AD_probe_pin);  // A1 vstup
      AD_volt = (AD_in * 5.0) / 1024.0;  // převod 0-1024 na 0.0-5.0V
      delay(1);
    #endif    
} // end void

//**********************************************************************************************
// eeprom pamet ********************************************************************************
void write_eeprom_long(int adres, long hodnota){ // zapis do pameti eeprom (long cislo)
  byte Hi = (hodnota & 0xFF);
  byte Lo = ((hodnota >> 8) & 0xFF);
  EEPROM.write(adres, Hi);
  EEPROM.write(adres + 1, Lo);
} // end void

void write_eeprom_byte(int adres, byte hodnota){ // zapis do pameti eeprom (byte cislo)
  EEPROM.write(adres, hodnota);
} // end void

long read_eeprom_long(long adr){ // cteni z pameti eeprom (long cislo)
  long Hig = EEPROM.read(adr);
  long Low = EEPROM.read(adr + 1);
  return ((Hig << 0) & 0xFF) + ((Low << 8) & 0xFFFF); // vraci long cislo ze dvou bunek eeprom
} // end void

long read_eeprom_byte(long adr){ // cteni z pameti eeprom (byte cislo)
  byte High = EEPROM.read(adr);
  return (High); // vraci byte cislo z eeprom
} // end void
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

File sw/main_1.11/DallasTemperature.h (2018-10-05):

#ifndef DallasTemperature_h
#define DallasTemperature_h

#define DALLASTEMPLIBVERSION "3.7.3"

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
// set to true to include code for new and delete operators
#ifndef REQUIRESNEW
#define REQUIRESNEW false
#endif

// set to true to include code implementing alarm search functions
#ifndef REQUIRESALARMS
#define REQUIRESALARMS true
#endif

#include <inttypes.h>
#include "OneWire.h"

// Model IDs
#define DS18S20MODEL 0x10  // also DS1820
#define DS18B20MODEL 0x28
#define DS1822MODEL  0x22
#define DS1825MODEL  0x3B

// OneWire commands
#define STARTCONVO      0x44  // Tells device to take a temperature reading and put it on the scratchpad
#define COPYSCRATCH     0x48  // Copy EEPROM
#define READSCRATCH     0xBE  // Read EEPROM
#define WRITESCRATCH    0x4E  // Write to EEPROM
#define RECALLSCRATCH   0xB8  // Reload from last known
#define READPOWERSUPPLY 0xB4  // Determine if device needs parasite power
#define ALARMSEARCH     0xEC  // Query bus for devices with an alarm condition

// Scratchpad locations
#define TEMP_LSB        0
#define TEMP_MSB        1
#define HIGH_ALARM_TEMP 2
#define LOW_ALARM_TEMP  3
#define CONFIGURATION   4
#define INTERNAL_BYTE   5
#define COUNT_REMAIN    6
#define COUNT_PER_C     7
#define SCRATCHPAD_CRC  8

// Device resolution
#define TEMP_9_BIT  0x1F //  9 bit
#define TEMP_10_BIT 0x3F // 10 bit
#define TEMP_11_BIT 0x5F // 11 bit
#define TEMP_12_BIT 0x7F // 12 bit

// Error Codes
#define DEVICE_DISCONNECTED_C -127
#define DEVICE_DISCONNECTED_F -196.6
#define DEVICE_DISCONNECTED_RAW -7040

typedef uint8_t DeviceAddress[8];

class DallasTemperature
{
public:

    DallasTemperature();
    DallasTemperature(OneWire*);

    void setOneWire(OneWire*);

    // initialise bus
    void begin(void);

    // returns the number of devices found on the bus
    uint8_t getDeviceCount(void);

    // returns true if address is valid
    bool validAddress(const uint8_t*);

    // finds an address at a given index on the bus
    bool getAddress(uint8_t*, uint8_t);

    // attempt to determine if the device at the given address is connected to the bus
    bool isConnected(const uint8_t*);

    // attempt to determine if the device at the given address is connected to the bus
    // also allows for updating the read scratchpad
    bool isConnected(const uint8_t*, uint8_t*);

    // read device's scratchpad
    bool readScratchPad(const uint8_t*, uint8_t*);

    // write device's scratchpad
    void writeScratchPad(const uint8_t*, const uint8_t*);

    // read device's power requirements
    bool readPowerSupply(const uint8_t*);

    // get global resolution
    uint8_t getResolution();

    // set global resolution to 9, 10, 11, or 12 bits
    void setResolution(uint8_t);

    // returns the device resolution: 9, 10, 11, or 12 bits
    uint8_t getResolution(const uint8_t*);

    // set resolution of a device to 9, 10, 11, or 12 bits
    bool setResolution(const uint8_t*, uint8_t);

    // sets/gets the waitForConversion flag
    void setWaitForConversion(bool);
    bool getWaitForConversion(void);

    // sets/gets the checkForConversion flag
    void setCheckForConversion(bool);
    bool getCheckForConversion(void);

    // sends command for all devices on the bus to perform a temperature conversion
    void requestTemperatures(void);

    // sends command for one device to perform a temperature conversion by address
    bool requestTemperaturesByAddress(const uint8_t*);

    // sends command for one device to perform a temperature conversion by index
    bool requestTemperaturesByIndex(uint8_t);

    // returns temperature raw value (12 bit integer of 1/16 degrees C)
    int16_t getTemp(const uint8_t*);

    // returns temperature in degrees C
    float getTempC(const uint8_t*);

    // returns temperature in degrees F
    float getTempF(const uint8_t*);

    // Get temperature for device index (slow)
    float getTempCByIndex(uint8_t);

    // Get temperature for device index (slow)
    float getTempFByIndex(uint8_t);

    // returns true if the bus requires parasite power
    bool isParasitePowerMode(void);

    bool isConversionAvailable(const uint8_t*);

#if REQUIRESALARMS

    typedef void AlarmHandler(const uint8_t*);

    // sets the high alarm temperature for a device
    // accepts a char.  valid range is -55C - 125C
    void setHighAlarmTemp(const uint8_t*, char);

    // sets the low alarm temperature for a device
    // accepts a char.  valid range is -55C - 125C
    void setLowAlarmTemp(const uint8_t*, char);

    // returns a signed char with the current high alarm temperature for a device
    // in the range -55C - 125C
    char getHighAlarmTemp(const uint8_t*);

    // returns a signed char with the current low alarm temperature for a device
    // in the range -55C - 125C
    char getLowAlarmTemp(const uint8_t*);

    // resets internal variables used for the alarm search
    void resetAlarmSearch(void);

    // search the wire for devices with active alarms
    bool alarmSearch(uint8_t*);

    // returns true if ia specific device has an alarm
    bool hasAlarm(const uint8_t*);

    // returns true if any device is reporting an alarm on the bus
    bool hasAlarm(void);

    // runs the alarm handler for all devices returned by alarmSearch()
    void processAlarms(void);

    // sets the alarm handler
    void setAlarmHandler(const AlarmHandler *);

    // The default alarm handler
    static void defaultAlarmHandler(const uint8_t*);

#endif

    // if no alarm handler is used the two bytes can be used as user data
    // example of such usage is an ID.
    // note if device is not connected it will fail writing the data.
    // note if address cannot be found no error will be reported.
    // in short use carefully
    void setUserData(const uint8_t*, int16_t );
    void setUserDataByIndex(uint8_t, int16_t );
    int16_t getUserData(const uint8_t* );
    int16_t getUserDataByIndex(uint8_t );

    // convert from Celsius to Fahrenheit
    static float toFahrenheit(float);

    // convert from Fahrenheit to Celsius
    static float toCelsius(float);

    // convert from raw to Celsius
    static float rawToCelsius(int16_t);

    // convert from raw to Fahrenheit
    static float rawToFahrenheit(int16_t);

#if REQUIRESNEW

    // initialize memory area
    void* operator new (unsigned int);

    // delete memory reference
    void operator delete(void*);

#endif
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

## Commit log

2018-10-01 Create project
    [BOM-UNO florist automata V1.0.csv, UNO florist automata V1.0.brd, UNO florist automata V1.0.sch]
2019-02-22 Přidaná verze HW a FW 1.10
    [BOM-UNO florist automata V1.0.csv, BOM-UNO florist automata V1.10.csv, UNO florist automata V1.0.brd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]

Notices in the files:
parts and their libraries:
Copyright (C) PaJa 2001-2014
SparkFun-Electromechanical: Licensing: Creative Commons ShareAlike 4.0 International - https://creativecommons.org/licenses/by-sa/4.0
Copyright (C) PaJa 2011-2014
